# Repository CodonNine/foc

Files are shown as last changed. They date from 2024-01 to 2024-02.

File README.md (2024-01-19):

# 三相逆变器驱动板
## 1.设计指标
- 输入电压：24V-48V DC
- 输出电压：24V(RMS) AC
- 频率：50-60Hz
- 输出功率：60W
- 额定电流：10A

## 2.附加接口
- 一路5V-1A输出
- 输入电压分压采样输出
- 输出电压分压采样输出（加偏置）
- 三相桥低侧电流采样放大输出（加偏置）
- 带光耦隔离的三相PWM信号输入

## 3.元件选型
- 偏置电源：LP3985
- MOSFET：NCEP023N10 100V 300A
- 三相桥驱动器：eg2133
- 12V电源芯片：eg1198
- 5V电源芯片：ln3492
- 光耦：PC817

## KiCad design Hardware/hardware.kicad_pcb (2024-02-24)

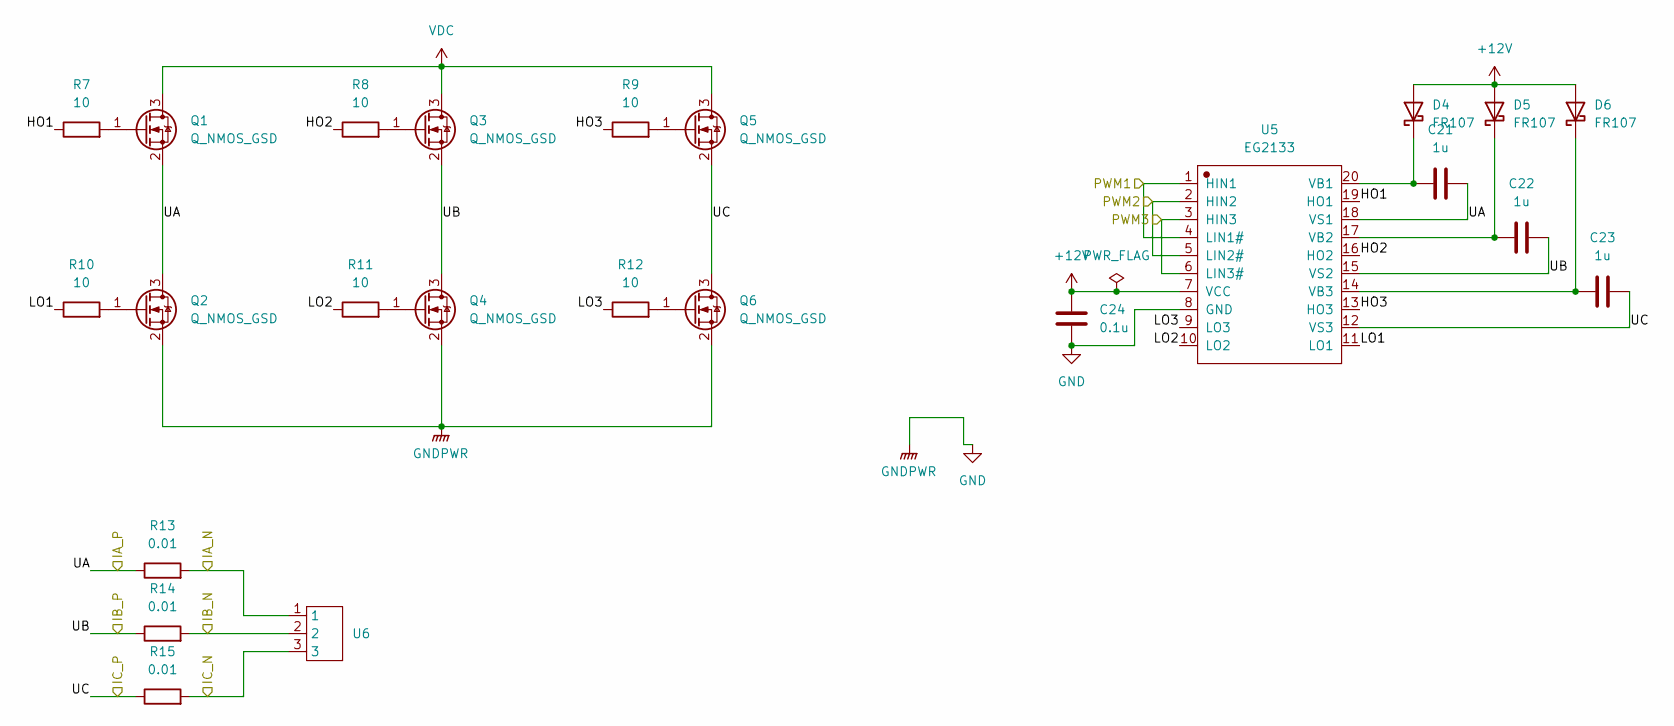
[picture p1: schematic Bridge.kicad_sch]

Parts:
C21, C22, C23: 1u; C_0603_1608Metric
C24: 0.1u; C_0603_1608Metric
D4, D5, D6: FR107; D_SOD-123F
Q1, Q2, Q3, Q4, Q5, Q6: Q_NMOS_GSD; Infineon_PG-HSOF-8-1
R7, R8, R9, R10, R11, R12: 10; R_0603_1608Metric
R13, R14, R15: 0.01; R_2512_6332Metric
U5: EG2133; TSSOP-20_4.4x6.5mm_P0.65mm
U6: KF301-3P

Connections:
+12V: C24.1, D4.2 (A), D5.2 (A), D6.2 (A), U5.7 (VCC); also elsewhere on the board
/Bridge/HO1: R7.1, U5.19 (HO1)
/Bridge/HO2: R8.1, U5.16 (HO2)
/Bridge/HO3: R9.1, U5.13 (HO3)
/Bridge/IA_N: R13.2, U6.1; also elsewhere on the board
/Bridge/IB_N: R14.2, U6.2; also elsewhere on the board
/Bridge/IC_N: R15.2, U6.3; also elsewhere on the board
/Bridge/LO1: R10.1, U5.11 (LO1)
/Bridge/LO2: R11.1, U5.10 (LO2)
/Bridge/LO3: R12.1, U5.9 (LO3)
/Bridge/PWM1: U5.1 (HIN1), U5.4 (LIN1#); also elsewhere on the board
/Bridge/PWM2: U5.2 (HIN2), U5.5 (LIN2#); also elsewhere on the board
/Bridge/PWM3: U5.3 (HIN3), U5.6 (LIN3#); also elsewhere on the board
/Bridge/UA: C21.1, Q1.2 (S), Q2.3 (D), R13.1, U5.18 (VS1); also elsewhere on the board
/Bridge/UB: C22.1, Q3.2 (S), Q4.3 (D), R14.1, U5.15 (VS2); also elsewhere on the board
/Bridge/UC: C23.1, Q5.2 (S), Q6.3 (D), R15.1, U5.12 (VS3); also elsewhere on the board
GND: C24.2, Q2.2 (S), Q4.2 (S), Q6.2 (S), U5.8 (GND); also elsewhere on the board
unnamed: C21.2, D4.1 (K), U5.20 (VB1)
unnamed: C22.2, D5.1 (K), U5.17 (VB2)
unnamed: C23.2, D6.1 (K), U5.14 (VB3)
unnamed: Q1.1 (G), R7.2
unnamed: Q2.1 (G), R10.2
unnamed: Q3.1 (G), R8.2
unnamed: Q4.1 (G), R11.2
unnamed: Q5.1 (G), R9.2
unnamed: Q6.1 (G), R12.2
VDC: Q1.3 (D), Q3.3 (D), Q5.3 (D); also elsewhere on the board

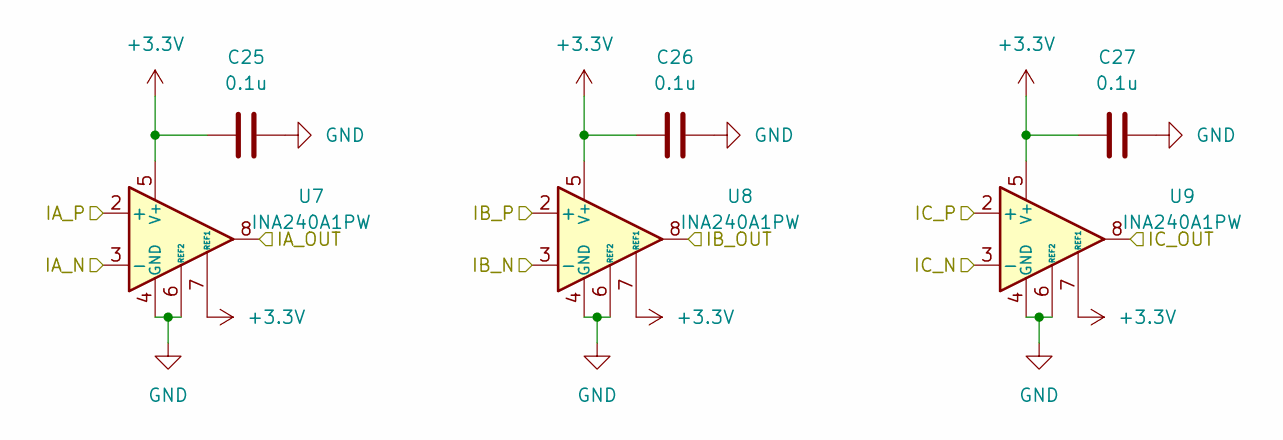
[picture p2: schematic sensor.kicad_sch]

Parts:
C25, C26, C27: 0.1u; C_0603_1608Metric
U7, U8, U9: INA240A1PW; TSSOP-8_4.4x3mm_P0.65mm

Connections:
+3.3V: C25.1, C26.1, C27.1, U7.5 (V+), U7.7 (REF1), U8.5 (V+), U8.7 (REF1), U9.5 (V+), U9.7 (REF1); also elsewhere on the board
/Bridge/IA_N: U7.3 (-); also elsewhere on the board
/Bridge/IB_N: U8.3 (-); also elsewhere on the board
/Bridge/IC_N: U9.3 (-); also elsewhere on the board
/Bridge/UA: U7.2 (+); also elsewhere on the board
/Bridge/UB: U8.2 (+); also elsewhere on the board
/Bridge/UC: U9.2 (+); also elsewhere on the board
/interface/IA_OUT: U7.8; also elsewhere on the board
/interface/IB_OUT: U8.8; also elsewhere on the board
/interface/IC_OUT: U9.8; also elsewhere on the board
GND: C25.2, C26.2, C27.2, U7.1 (GND), U7.4 (GND), U7.6 (REF2), U8.1 (GND), U8.4 (GND), U8.6 (REF2), U9.1 (GND), U9.4 (GND), U9.6 (REF2); also elsewhere on the board

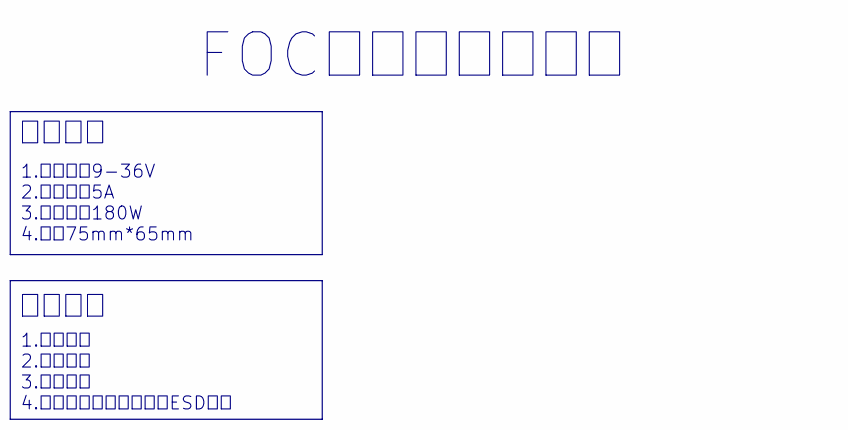
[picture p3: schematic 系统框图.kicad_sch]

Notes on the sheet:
1.输入电压9-36V 2.额定电流5A 3.最大功率180W 4.尺寸75mm*65mm
1.过流保护 2.过压保护 3.欠压保护 4.信号输入和输出线上的ESD防护
FOC控制器设计纲要
额定参数
保护措施

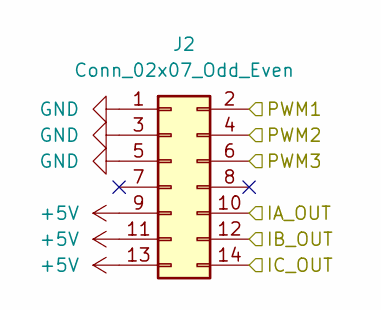
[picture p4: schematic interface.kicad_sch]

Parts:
J2: Conn_02x07_Odd_Even; PinHeader_2x07_P2.54mm_Vertical

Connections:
+5V: J2.9, J2.11, J2.13; also elsewhere on the board
/Bridge/PWM1: J2.2; also elsewhere on the board
/Bridge/PWM2: J2.4; also elsewhere on the board
/Bridge/PWM3: J2.6; also elsewhere on the board
/interface/IA_OUT: J2.10; also elsewhere on the board
/interface/IB_OUT: J2.12; also elsewhere on the board
/interface/IC_OUT: J2.14; also elsewhere on the board
GND: J2.1, J2.3, J2.5; also elsewhere on the board

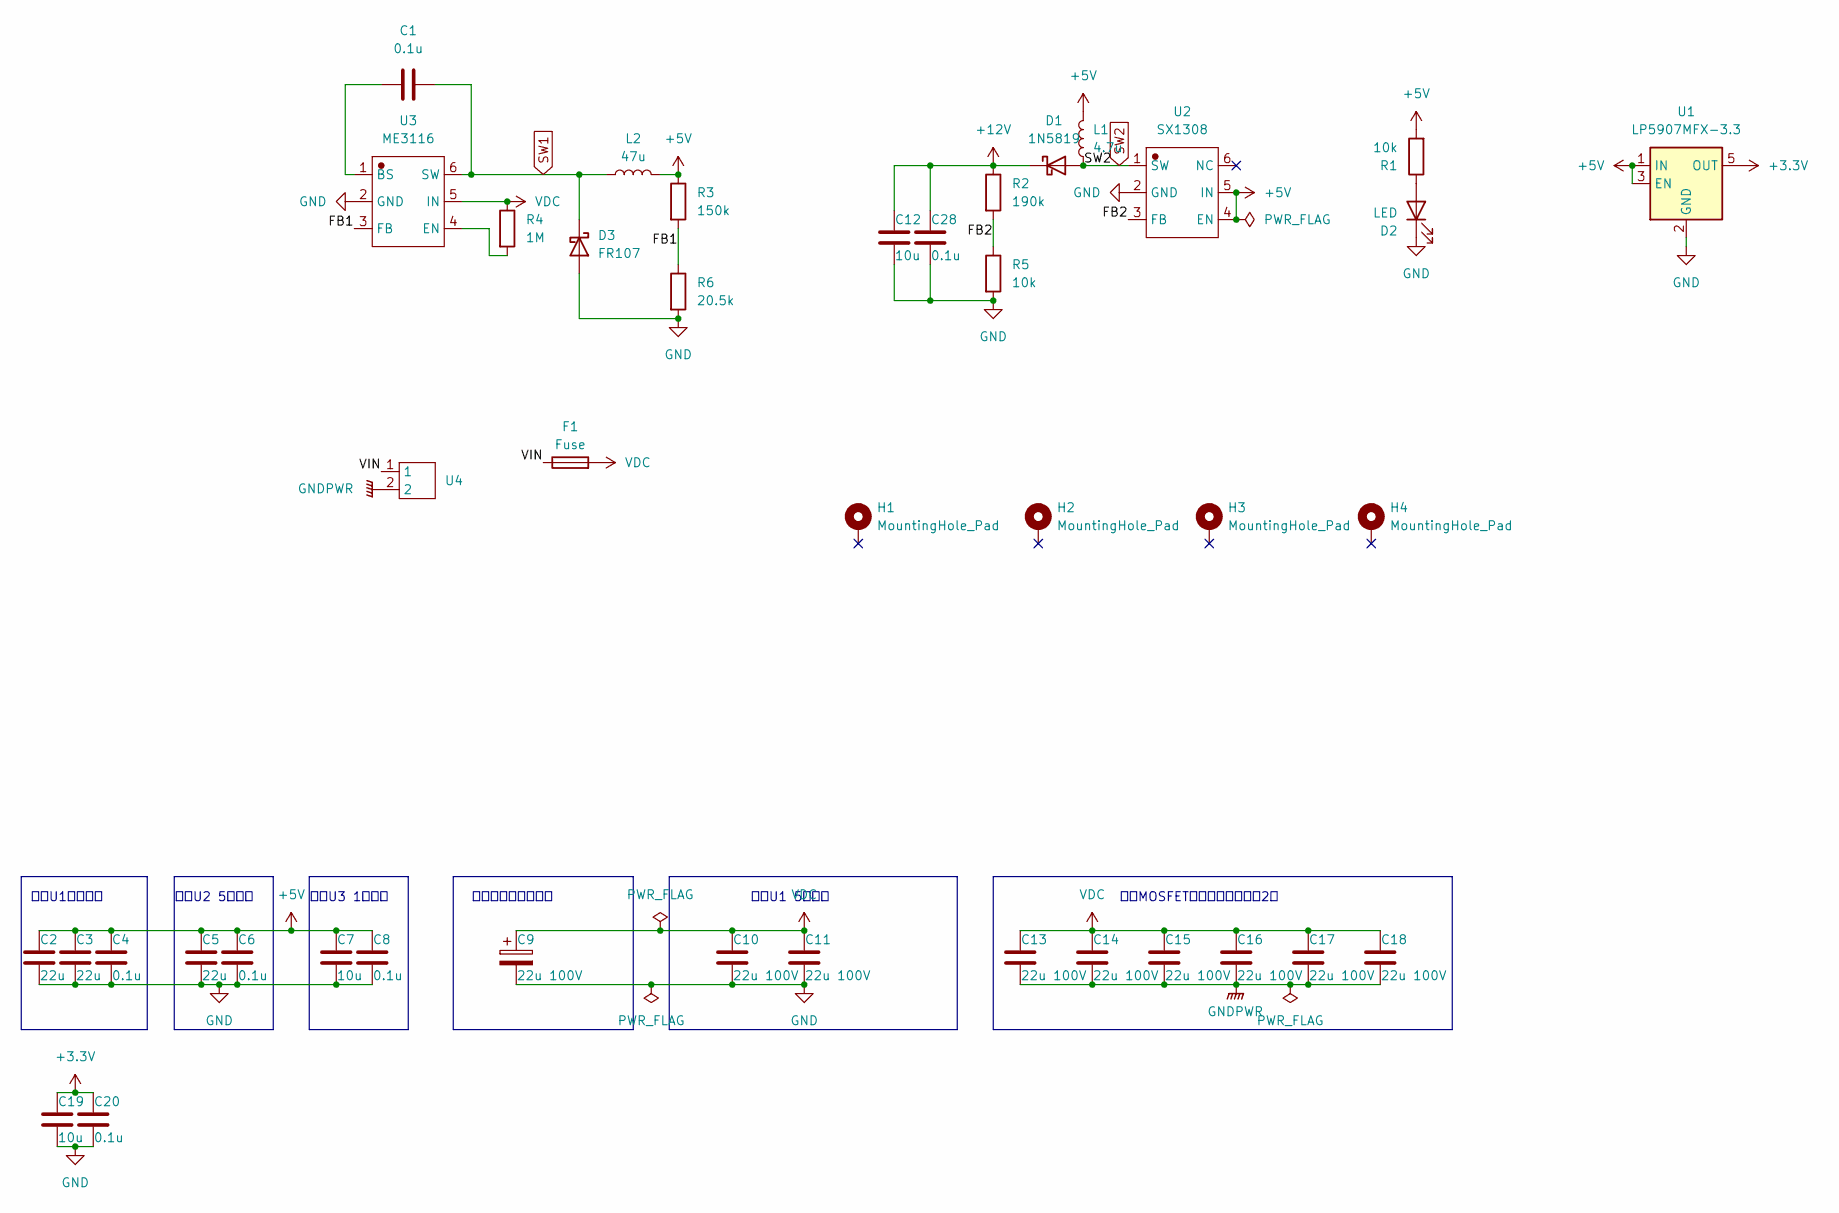
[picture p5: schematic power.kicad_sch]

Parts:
C1, C4, C6, C8, C20, C28: 0.1u; C_0603_1608Metric
C2, C3, C5: 22u; C_0603_1608Metric
C7, C12, C19: 10u; C_0603_1608Metric
C9: 22u 100V
C10, C11, C13, C14, C15, C16, C17, C18: 22u 100V; C_1206_3216Metric
D1: 1N5819; D_SOD-123
D2: LED; LED_0603_1608Metric
D3: FR107; D_SOD-123F
F1: Fuse; 1808-FuseBase-SMD
H1, H2, H3, H4: MountingHole_Pad; MountingHole_3.2mm_M3_Pad_Via
L1: 4.7u; L_Chilisin_BMRA00040420
L2: 47u; L_Chilisin_BMRA00040420
R1, R5: 10k; R_0603_1608Metric
R2: 190k; R_0603_1608Metric
R3: 150k; R_0603_1608Metric
R4: 1M; R_0603_1608Metric
R6: 20.5k; R_0603_1608Metric
U1: LP5907MFX-3.3; SOT-23-5
U2: SX1308; SOT-23-6
U3: ME3116; SOT-23-6
U4: KF301-2P

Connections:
+3.3V: C19.2, C20.2, U1.5 (OUT); also elsewhere on the board
+5V: C2.2, C3.2, C4.2, C5.2, C6.2, C7.2, C8.2, L1.2, L2.2, R1.2, R3.1, U1.1 (IN), U1.3 (EN), U2.4 (EN), U2.5 (IN); also elsewhere on the board
+12V: C12.2, C28.2, D1.1 (K), R2.1; also elsewhere on the board
/power/FB1: R3.2, R6.1, U3.3 (FB)
/power/FB2: R2.2, R5.1, U2.3 (FB)
/power/VIN: F1.1, U4.1
GND: C2.1, C3.1, C4.1, C5.1, C6.1, C7.1, C8.1, C9.2, C10.1, C11.1, C12.1, C13.1, C14.1, C15.1, C16.1, C17.1, C18.1, C19.1, C20.1, C28.1, D2.1 (K), D3.2 (A), R5.2, R6.2, U1.2 (GND), U2.2 (GND), U3.2 (GND), U4.2; also elsewhere on the board
unnamed: D2.2 (A), R1.1
unnamed: C1.1, U3.1 (BS)
unnamed: R4.2, U3.4 (EN)
SW1: C1.2, D3.1 (K), L2.1, U3.6 (SW)
SW2: D1.2 (A), L1.1, U2.1 (SW)
VDC: C9.1, C10.2, C11.2, C13.2, C14.2, C15.2, C16.2, C17.2, C18.2, F1.2, R4.1, U3.5 (IN); also elsewhere on the board

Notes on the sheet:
靠近U3 1脚放置
靠近U2 5脚放置
靠近输入保险丝放置
靠近U1 5脚放置
靠近MOSFET上桥臂放置，每管2个
靠近U1输出电感

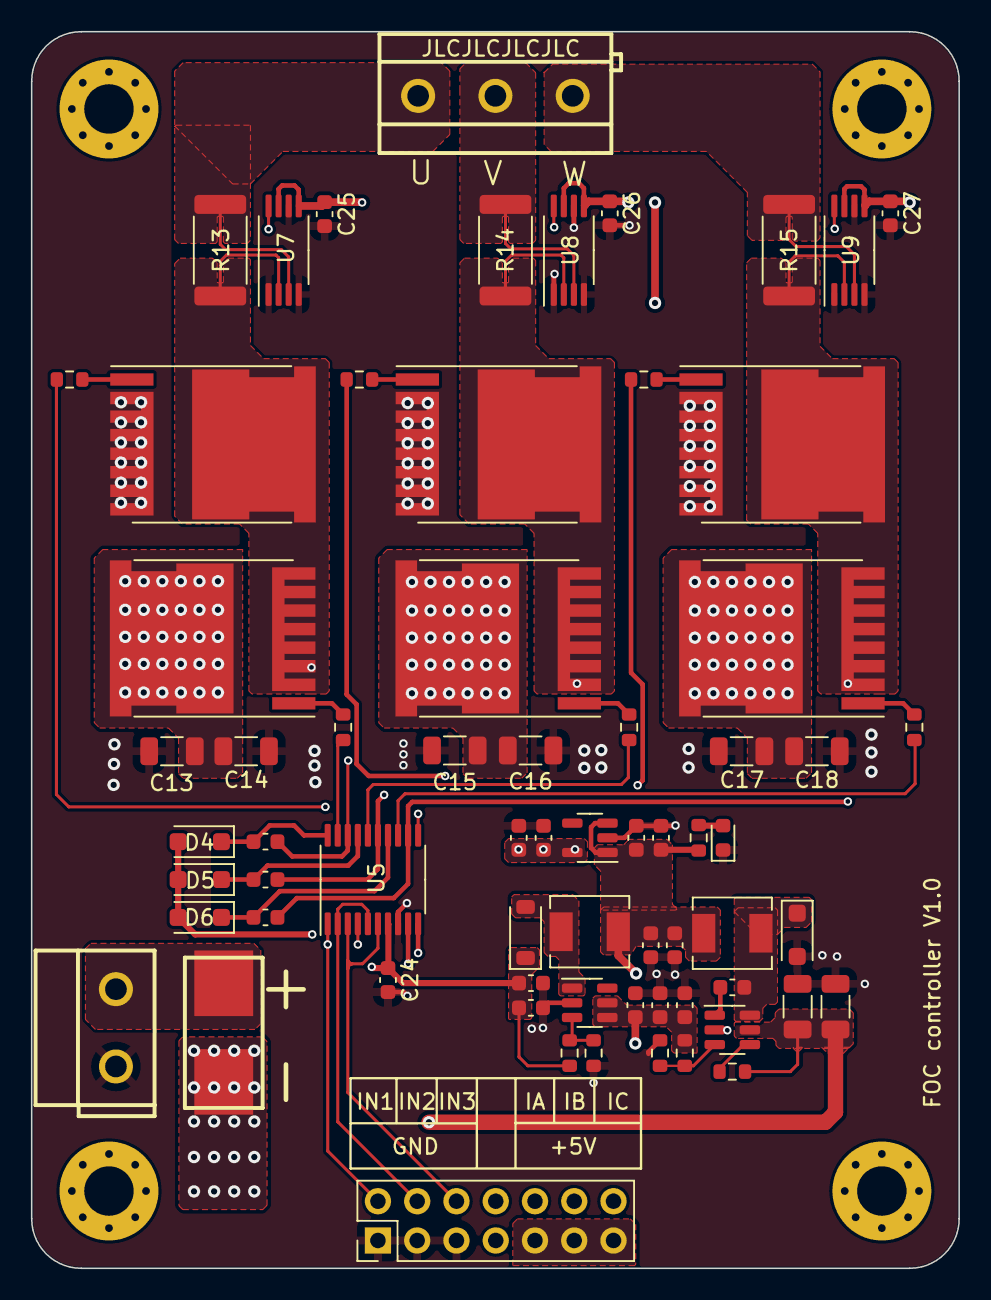
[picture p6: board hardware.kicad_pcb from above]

Board: 4 copper layers, 60.0 x 80.0 mm, 71 parts (0 on the bottom side), 40 nets.
